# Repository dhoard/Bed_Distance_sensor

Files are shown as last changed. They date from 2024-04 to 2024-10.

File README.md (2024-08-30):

##  The Future of 3D printer Bed Leveling

[BDsensor](https://www.pandapi3d.com/bdsensor) is the first distance sensor that can work with 3D printer and do fast bed leveling and adjust z axis in real time.
it can measure the bed distance at any point in real time without moving the z axis up and down.

Faster leveling, realtime compensation, high accuracy.

1. No need to do probe points before every print, it will be automatically compensated for based on actual distance in real time.
 
2. You can do bed mesh leveling like a normal proximity sensor but much faster with this BDsensor.
   
3. Easy manual bed level adjustment thanks to ability to display the live sensor distance measurement on your screen.

Sensor type: inductive, eddy, can only measure the metal plate.

Range: 4mm (for different metal the range should be different, the normal pei steel plate is 4mm, but aluminum is about 2mm)

### Hardware:
* It can connect to most motherboards or GPIOs on the RaspberryPi
* Easy to install:
  small and light; can be installed anywhere, even surrounding metal above
* Support Can bus module
* Support high temperature chamber(120C) with the long cable probe [BDsensorM](https://github.com/markniu/Bed_Distance_sensor/wiki/BDsensor-M).
### Hardware Version
 . | hardware | firmware
--- | --- |---  
2022.6 | BDsensor VA, V1.0 | V1.0  
2023.4 | BDsensor VB, V1.1, the connector was changed | V1.1, support self reboot
2023.11 | BDsensor VB, V1.3, Upgrade the MCU to STM32 | V1.2, for stm32
2024.2  |              |V1.2c, [Support nozzle collision sensing](https://github.com/markniu/Bed_Distance_sensor/wiki/Collision-sensing)
2024.3  | BDsensorM V1.0             | V1.2c
2024.7  | BDsensorM V1.1             |  V1.2c, [Pins order](https://github.com/markniu/Bed_Distance_sensor/issues/178#issuecomment-2319621934) are changed in EXP1 connector

### Software
 . | Marlin | Klipper
--- | --- |---  
Real Time leveling(beta) |:heavy_check_mark:| :heavy_check_mark:  
Fast bed mesh |:heavy_check_mark:| :heavy_check_mark: 
Fast bed mesh(No toolhead stop)|:heavy_check_mark: | :heavy_check_mark: 
Distance display |:heavy_check_mark: | :heavy_check_mark: 
Can bus toolhead|No | :heavy_check_mark: 
standby mode automatic while printing|:heavy_check_mark: | :heavy_check_mark: 
[KAMP](https://github.com/kyleisah/Klipper-Adaptive-Meshing-Purging) Adaptive Meshing & Purging |No | :heavy_check_mark: 
nozzle collision sensing|[Detail](https://github.com/markniu/Bed_Distance_sensor/wiki/Collision-sensing-for-Marlin):heavy_check_mark:  | :heavy_check_mark: 

### Benefit of Collision sensing
1.  **Auto z offset calibration**.
2.  **Overcome the temperature drift**.
     The temperature drift will only change the z_offset, it will rise or low the whole bed mesh, but does not change the bed mesh with this BDsensor. that means the bed mesh is the same even with [different temperature](https://www.pandapi3d.com/post/nozzle-collision-sensing-with-bdsensor).
3. Repeatability: **+/-0.005mm**
4. No external hardware and easy to adjust

### Benefit of version M:

1.  For High temperature chamber up to [120C](https://github.com/markniu/Bed_Distance_sensor/wiki/BDsensor-M)
2.  The lightest probe, 1.5g

### Document  : [WiKi](https://github.com/markniu/Bed_Distance_sensor/wiki)

[History](https://hackaday.io/project/185096-0006mm-distance-resolution-sensor-for-3d-printer)

#### Mount STL:  [BLtouch_Compatible](https://www.thingiverse.com/thing:6098131) | [VzBoT](https://discord.com/channels/829828765512106054/1163237892957671424) | [Stealthburner Voron](https://www.printables.com/model/831679-lazy-bd-sensor-adapter-for-stealthburner-voron)

### Support
 https://www.facebook.com/groups/380795976169477

#### Where to buy:
 [pandapi3d.com](https://www.pandapi3d.com) , [elecrow](https://www.elecrow.com/bd-sensor.html) , [淘宝店](https://item.taobao.com/item.htm?spm=a1z10.1-c.w4004-14344044600.5.60a16ff77NRBL5&id=684572042388)

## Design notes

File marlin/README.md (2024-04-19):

Install marlin

https://github.com/markniu/Bed_Distance_sensor/wiki/Installing-Bed-Distance-Sensor

example: https://drive.google.com/drive/folders/13poitJhHradERgTLGtSDJb0zpuyNYHZY?usp=sharing

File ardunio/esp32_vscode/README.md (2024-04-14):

Arduino testing code

This is a simple arduino testing code. It read the distance data from BDsensor after initial the communication port.

If you want to do more code by yourself for other application here is the protocol of data 

https://github.com/markniu/Bed_Distance_sensor/wiki/Data-Protocol

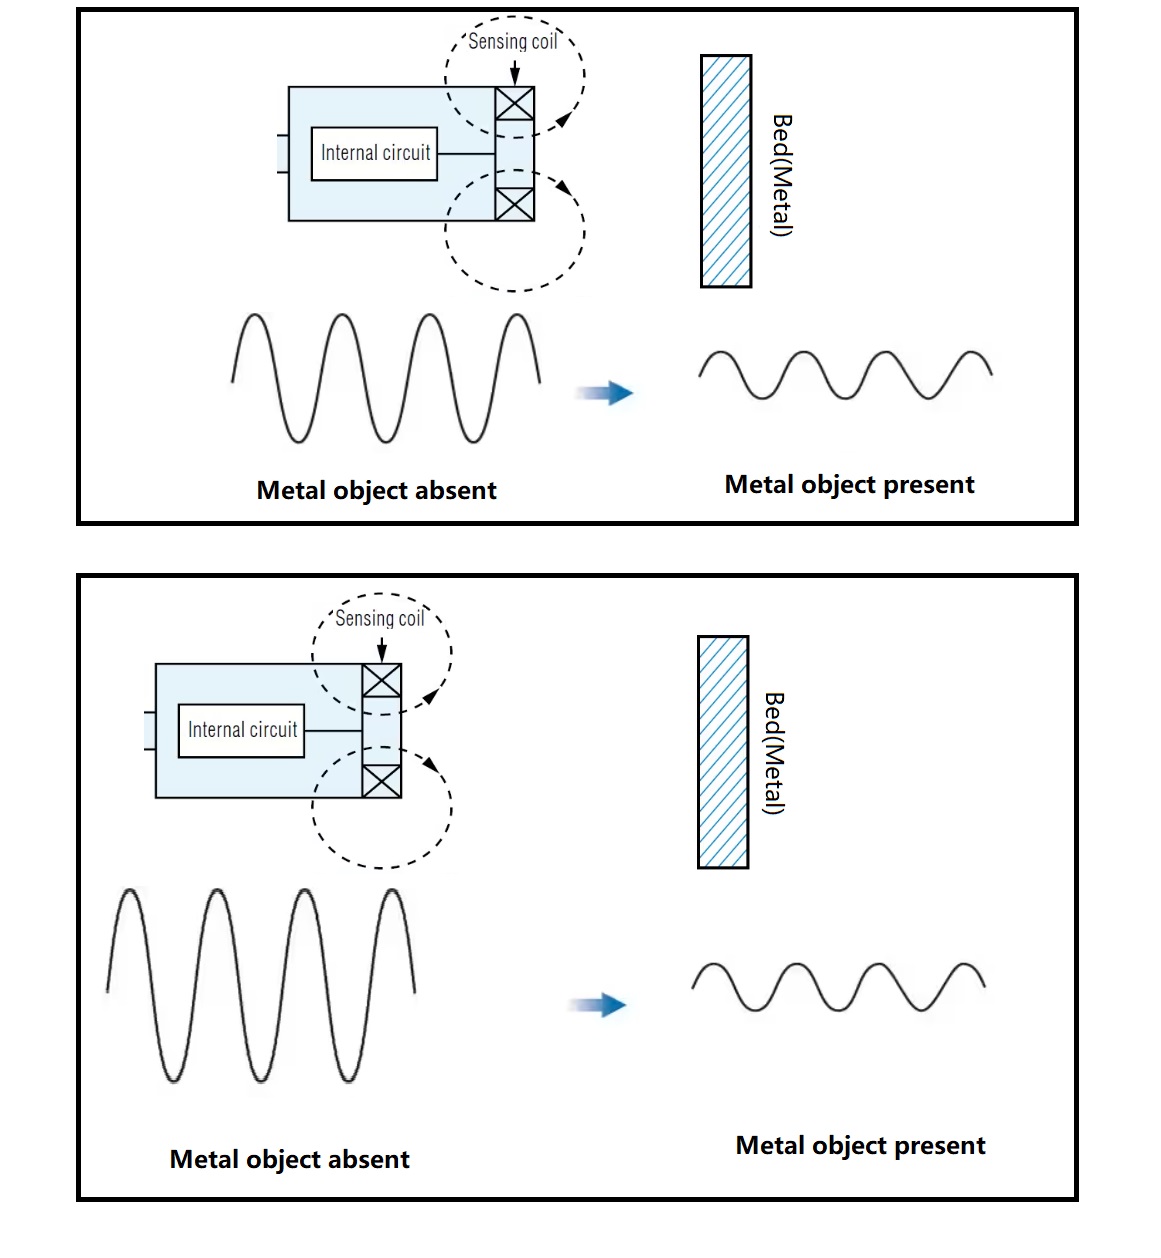
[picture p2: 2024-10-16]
doc/images/howwork.png

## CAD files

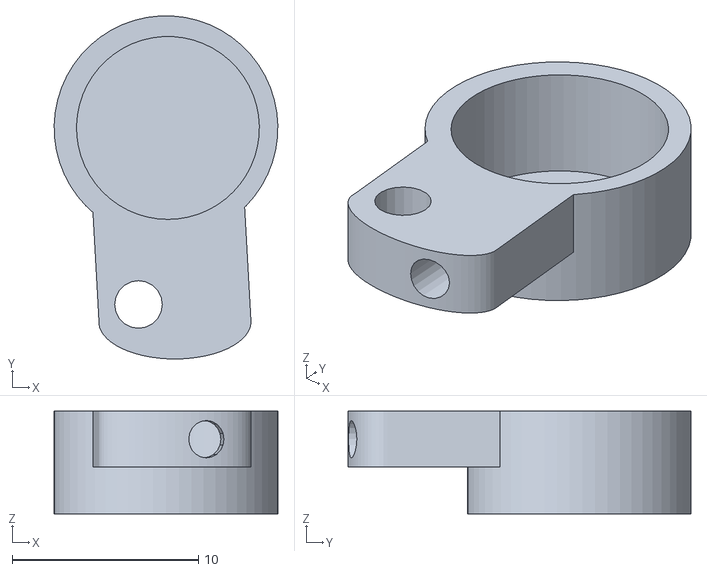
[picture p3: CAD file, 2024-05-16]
design/coil_case_without_coil.stl
12.0 x 18.4 x 5.50

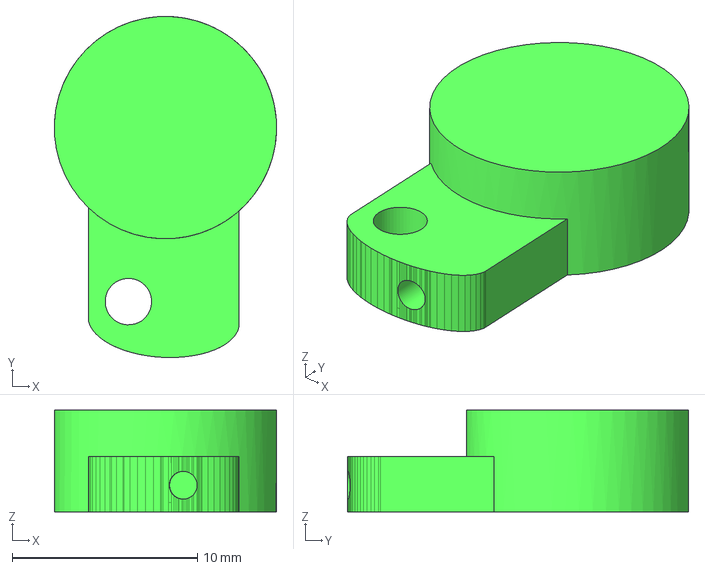
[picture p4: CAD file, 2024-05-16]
design/coil_case.step
12.0 x 18.4 x 5.50 mm

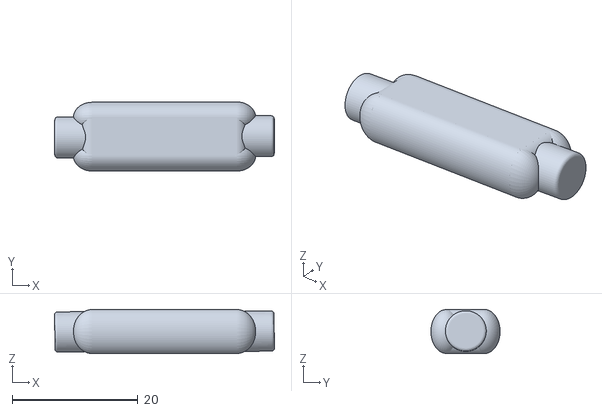
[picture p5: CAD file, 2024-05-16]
design/PCB_case.stl
35.0 x 11.0 x 7.00

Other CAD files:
design/coil_case.stl

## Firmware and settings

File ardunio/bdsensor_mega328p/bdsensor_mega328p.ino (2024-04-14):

#include <Arduino.h>
#include <U8g2lib.h>
#include "Panda_segmentBed_I2C.h"
#ifdef U8X8_HAVE_HW_SPI
#include <SPI.h>
#endif
#ifdef U8X8_HAVE_HW_I2C
#include <Wire.h>
#endif

I2C_SegmentBED BD_SENSOR_I2C;
#define  I2C_BED_SDA  12  
#define  I2C_BED_SCL  11  
#define DELAY 100
#define MAX_BD_HEIGHT 6.9
#define CMD_START_READ_CALIBRATE_DATA   1017
#define CMD_END_READ_CALIBRATE_DATA   1018
#define CMD_START_CALIBRATE 1019
#define CMD_END_CALIBRATE 1021  
#define CMD_READ_VERSION  1016
#define CMD_DISTANCD_RAWDATA_TYPE 1020       // switch output distance data type to raw data, default is mm (1 represent 0.01mm)

char tmp_1[50];
unsigned int n=0,i=0;
float Distance=0.0;

U8G2_SSD1306_128X32_UNIVISION_F_SW_I2C u8g2(U8G2_R0, /* clock=*/ SCL, /* data=*/ SDA, /* reset=*/ U8X8_PIN_NONE);  



void dis_text(char *tmp_d,char x,char y)
{
  
  u8g2.setFont(u8g2_font_ncenB08_tr); // choose a suitable font
  u8g2.drawStr(x,y,tmp_d);  // write something to the internal memory
  u8g2.sendBuffer();          // transfer internal memory to the display

}

unsigned short read_one_data()
{
    unsigned short tmp=0;
    tmp=BD_SENSOR_I2C.BD_i2c_read();    
    if(BD_SENSOR_I2C.BD_Check_OddEven(tmp)==0)
      //printf("CRC error!\n");
     // sprintf(tmp_1,"CRC error");
       tmp=1024;
    else
    {
      tmp=(tmp&0x3ff);
     // sprintf(tmp_1,"Distance:%.2f\n",Distance);
      //printf(tmp_1);
    }
    return tmp;
}

void read_version(char *txt)
{
  int i=0;
  BD_SENSOR_I2C.BD_i2c_write(CMD_READ_VERSION);
  for(i=0;i<20;i++)
      txt[i]=read_one_data();
  BD_SENSOR_I2C.BD_i2c_write(CMD_END_READ_CALIBRATE_DATA);
}


unsigned short read_raw_data(void)
{
  unsigned short tm=0;
  BD_SENSOR_I2C.BD_i2c_write(CMD_DISTANCD_RAWDATA_TYPE);
  tm=read_one_data();
  BD_SENSOR_I2C.BD_i2c_write(CMD_END_READ_CALIBRATE_DATA);
  return tm;
}

void setup(void) {
  u8g2.begin();
  u8g2.clearBuffer();          // clear the internal memory
  BD_SENSOR_I2C.i2c_init(I2C_BED_SDA,I2C_BED_SCL,0x3C,20);
  BD_SENSOR_I2C.BD_i2c_write(CMD_END_READ_CALIBRATE_DATA);
   //read and display version
  sprintf(tmp_1,"");
  read_version(tmp_1+strlen(tmp_1));
  dis_text(tmp_1,0,10);
  ///
  
}

void loop(void) {
  u8g2.clearBuffer(); 
  u8g2.setFont(u8g2_font_ncenB08_tr); // choose a suitable font
  //u8g2.drawStr(x,y,tmp_d);  // write something to the internal memory
  //u8g2.sendBuffer();   

  sprintf(tmp_1,"");
  read_version(tmp_1+strlen(tmp_1));
  //dis_text(tmp_1,0,10);
  u8g2.drawStr(0,10,tmp_1);
  
  //delay(10);  
  //read and display raw data
  n=read_raw_data();
  sprintf(tmp_1,"%d ",n);
  //dis_text(tmp_1,0,30);

  // read and display distance,but need to calibrate first
  Distance=read_one_data()/100.0;
  sprintf(tmp_1+strlen(tmp_1),", ");
  dtostrf(Distance, 5, 2, tmp_1+strlen(tmp_1));
  sprintf(tmp_1+strlen(tmp_1)," mm");
  u8g2.drawStr(0,30,tmp_1);
  u8g2.sendBuffer();
  //dis_text(tmp_1,0,30);

}

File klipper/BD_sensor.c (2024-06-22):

// Code for Bed Distance Sensor
// Mark yue<niujl123@sina.com>
// This file may be distributed under the terms of the GNU GPLv3 license.

#include <string.h>
#include <stdlib.h>
#include "board/gpio.h"
#include "board/irq.h"
#include "board/misc.h"
#include "command.h"
#include "sched.h"
#include "autoconf.h" // CONFIG_*
#include "basecmd.h" // oid_alloc
#include "board/gpio.h" // gpio_out_write
#include "board/irq.h" // irq_disable
#include "board/misc.h" // timer_is_before
#include "command.h" // DECL_COMMAND
#include "sched.h" // struct timer
#include "stepper.h" // stepper_event
#include "trsync.h" // trsync_add_signal

#define CMD_READ_DATA                 1015
#define CMD_READ_VERSION              1016
#define CMD_START_READ_CALIBRATE_DATA 1017
#define CMD_DISTANCE_MODE             1018
#define CMD_START_CALIBRATE           1019
#define CMD_END_CALIBRATE             1021
#define CMD_REBOOT_SENSOR             1022
#define CMD_SWITCH_MODE               1023
#define DATA_ERROR                    1024

#define CMD_Z_INDEX                    1025
#define CMD_CUR_Z                      1026
#define CMD_ADJ_Z                      1027
#define CMD_DIR_INV                    1028
#define CMD_STEP_MM                    1029
#define CMD_ZOID                       1030
#define CMD_RT_SAMPLE_TIME             1031
#define CMD_RT_RANGE                   1032


#define BYTE_CHECK_OK     0x01
#define BYTE_CHECK_ERR    0x00

#define BD_setLow(x)  gpio_out_write(x,0)
#define BD_setHigh(x) gpio_out_write(x,1)


uint8_t oid_g;
struct endstop {
    struct timer time;
    uint32_t rest_time, sample_time, nextwake,pin_num;
    struct trsync *ts;
    uint8_t flags, sample_count, trigger_count, trigger_reason;
    struct gpio_in pin;
};

enum { ESF_PIN_HIGH=1<<0, ESF_HOMING=1<<1 };

uint32_t delay_m = 20, homing_pose = 0;
int sda_pin = -1, scl_pin = -1, z_ofset = 0;
uint16_t BD_Data;
uint16_t BD_read_flag=CMD_DISTANCE_MODE;
int switch_mode = 0; //1:in switch mode
struct gpio_out sda_gpio, scl_gpio;
struct gpio_in sda_gpio_in;
static uint_fast8_t endstop_oversample_event(struct timer *t);
static struct endstop e ;

int z_index=0;
struct stepper {
    struct timer time;
    uint32_t interval;
    int16_t add;
    uint32_t count;
    uint32_t next_step_time, step_pulse_ticks;
    struct gpio_out step_pin, dir_pin;
    uint32_t position;
    struct move_queue_head mq;
    struct trsync_signal stop_signal;
    // gcc (pre v6) does better optimization when uint8_t are bitfields
    uint8_t flags : 8;
};
struct step_adjust{
    uint32_t cur_z;
    int adj_z_range;
    int invert_dir;
    int steps_per_mm;
    int step_time;
    int zoid;//oid for all the z stepper
};

#define NUM_Z_MOTOR  6
struct step_adjust step_adj[NUM_Z_MOTOR];//x,y,z
enum {
    SF_LAST_DIR=1<<0, SF_NEXT_DIR=1<<1, SF_INVERT_STEP=1<<2, SF_NEED_RESET=1<<3,
    SF_SINGLE_SCHED=1<<4, SF_HAVE_ADD=1<<5
};
struct endstop bd_tim ;

int32_t	diff_step=0,RT_SAMPLE_TIME=0,adjusted_step=0,RT_RANGE=1000;

int abs_bd(int a, int b){
 if (a > b)
    return a-b;
 else
 	return b-a;
}
extern void
command_config_stepper(uint32_t *args);
void adust_Z_live(uint16_t sensor_z);
void BD_i2c_write(unsigned int addr);
uint16_t BD_i2c_read(void);
void adust_Z_calc(uint16_t sensor_z,struct stepper *s);

void timer_bd_init(void);


int BD_i2c_init(uint32_t _sda,uint32_t _scl,
    uint32_t delays,uint32_t h_pose,int z_adjust)
{
    int i=0;
    sda_pin=_sda;
    scl_pin =_scl;
    homing_pose = h_pose;
    z_ofset = z_adjust;
    if (z_ofset > 500)
        z_ofset = 0;
    if(delays>0)
        delay_m=delays;
    sda_gpio=gpio_out_setup(sda_pin, 1);
    scl_gpio=gpio_out_setup(scl_pin, 1);

    gpio_out_write(sda_gpio, 1);
    gpio_out_write(scl_gpio, 1);
	for (i=0;i<NUM_Z_MOTOR;i++){
        step_adj[i].cur_z=0;
    	step_adj[i].zoid=0;
		step_adj[i].adj_z_range=0;
	}
    BD_i2c_write(CMD_REBOOT_SENSOR); //reset BDsensor
	////
 	if(CONFIG_CLOCK_FREQ>100000000)
		RT_SAMPLE_TIME= timer_from_us(11000);
	else if(CONFIG_CLOCK_FREQ>60000000)
		RT_SAMPLE_TIME= timer_from_us(16000);
	else //if(CONFIG_CLOCK_FREQ>60000000)
		RT_SAMPLE_TIME= timer_from_us(19000);
    return 1;
}

uint32_t nsecs_to_ticks_bd(uint32_t ns)
{
    return ns * (CONFIG_CLOCK_FREQ / 1000000);
}

void ndelay_bd_c(uint32_t nsecs)
{
   // if (CONFIG_MACH_AVR)
   //     return;
    uint32_t end = timer_read_time() + nsecs_to_ticks_bd(nsecs);
    while (timer_is_before(timer_read_time(), end));
       // irq_poll();
}

void ndelay_bd(uint32_t nsecs)
{
    int i=1;
    while(i--)
        ndelay_bd_c(nsecs);
}

unsigned short BD_Add_OddEven(unsigned short send_data)
{
    unsigned char i;
    unsigned char n;
    unsigned short out_data;
    n =0;
    for(i=0;i<10;i++){
        if(((send_data >>i)&0x01) == 0x01){
            n++;
        }
    }
    if((n&0x01) == 0x01){
        out_data = send_data | 0x400;
    }
    else{
        out_data = send_data | 0x00;
    }
    return out_data;
}

unsigned short BD_Check_OddEven(unsigned short rec_data)
{
    unsigned char i;
    unsigned char n;
    unsigned char ret;
    n =0;
    for(i=0;i<10;i++){
        if(((rec_data >>i)&0x01) == 0x01){
           n++;
        }
    }
    if((rec_data>>10) == (n&0x01)){
        ret = BYTE_CHECK_OK;
    }
    else{
        ret = BYTE_CHECK_ERR;
    }
    return ret;
}

void BD_I2C_start(void)
{
    sda_gpio=gpio_out_setup(sda_pin, 1);
    scl_gpio=gpio_out_setup(scl_pin, 1);
    BD_setHigh(scl_gpio);
    BD_setHigh(sda_gpio);
    ndelay_bd(delay_m);
    BD_setLow(sda_gpio);
    ndelay_bd(delay_m);
    BD_setLow(scl_gpio);
    ndelay_bd(delay_m);
}

void  BD_i2c_stop(void)
{
    ndelay_bd(delay_m);
    sda_gpio=gpio_out_setup(sda_pin, 1);
    BD_setLow(sda_gpio);
    ndelay_bd(delay_m);
    scl_gpio=gpio_out_setup(scl_pin, 1);
    BD_setHigh(scl_gpio);
    ndelay_bd(delay_m);

    BD_setHigh(sda_gpio);
    ndelay_bd(delay_m);
}

uint16_t BD_i2c_read(void)
{
    uint16_t b = DATA_ERROR;
    BD_I2C_start();
    BD_setHigh(sda_gpio);
    BD_setHigh(scl_gpio);
    ndelay_bd(delay_m);
    BD_setLow(scl_gpio);

    ndelay_bd(delay_m);
    b = 0;
    BD_setHigh(sda_gpio);
    sda_gpio_in=gpio_in_setup(sda_pin,0);
    for (unsigned char i = 0; i <= 10; i++) {
        b <<= 1;
        ndelay_bd(delay_m);
        BD_setHigh(scl_gpio);
		ndelay_bd(delay_m);
       // if (gpio_in_read(sda_gpio_in))
        b |= gpio_in_read(sda_gpio_in);
      //  ndelay_bd(delay_m);
        BD_setLow(scl_gpio);
    }
    BD_i2c_stop();
    if (BD_Check_OddEven(b) && (b & 0x3FF) < 1020){
        b = (b & 0x3FF);
        if(BD_read_flag==CMD_DISTANCE_MODE&&(b<1000)){
            b = b - z_ofset;
            if(b>DATA_ERROR)
                b=0;
        }

    }
    else
        b=DATA_ERROR;
 #if 0
    sda_gpio_in=gpio_in_setup(sda_pin,0);
    b=gpio_in_read(sda_gpio_in)*100;
 #endif
    return b;
}
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

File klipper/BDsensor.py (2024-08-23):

# Bed leveling sensor BDsensor(Bed Distance sensor)
# https://github.com/markniu/Bed_Distance_sensor
# Copyright (C) 2023 Mark yue <niujl123@sina.com>
# This file may be distributed under the terms of the GNU GPLv3 license.
import sched
import time
import copy
import chelper
import math
from threading import Timer
from mcu import MCU, MCU_trsync
from . import manual_probe
from . import probe
BD_TIMER = 0.600
TRSYNC_TIMEOUT = 0.025
TRSYNC_SINGLE_MCU_TIMEOUT = 0.250

CMD_READ_DATA = 1015
CMD_READ_VERSION = 1016
CMD_START_READ_CALIBRATE_DATA = 1017
CMD_DISTANCE_MODE = 1018
CMD_START_CALIBRATE = 1019
CMD_DISTANCE_RAWDATA_TYPE = 1020
CMD_END_CALIBRATE = 1021
CMD_REBOOT_SENSOR = 1022
CMD_SWITCH_MODE = 1023
DATA_ERROR = 1024

# Calculate a move's accel_t, cruise_t, and cruise_v
def calc_move_time(dist, speed, accel):
    axis_r = 1.
    if dist < 0.:
        axis_r = -1.
        dist = -dist
    if not accel or not dist:
        return axis_r, 0., dist / speed, speed
    max_cruise_v2 = dist * accel
    if max_cruise_v2 < speed ** 2:
        speed = math.sqrt(max_cruise_v2)
    accel_t = speed / accel
    accel_decel_d = accel_t * speed
    cruise_t = (dist - accel_decel_d) / speed
    return axis_r, accel_t, cruise_t, speed

# Helper to obtain a single probe measurement
def run_single_probe(probe, gcmd):
    probe_session = probe.start_probe_session(gcmd)
    probe_session.run_probe(gcmd)
    pos = probe_session.pull_probed_results()[0]
    probe_session.end_probe_session()
    return pos

# I2C BD_SENSOR
# devices connected to an MCU via an virtual i2c bus(2 any gpio)

HINT_TIMEOUT = """
If the probe did not move far enough to trigger, then
consider reducing the Z axis minimum position so the probe
can travel further (the Z minimum position can be negative).
"""


class BDPrinterProbe:
    def __init__(self, config, mcu_probe):
        self.printer = config.get_printer()
        self.name = config.get_name()
        self.config = config
        self.mcu_probe = mcu_probe
        self.speed = config.getfloat('speed', 5.0, above=0.)
        self.lift_speed = config.getfloat('lift_speed', self.speed, above=0.)
        self.x_offset = config.getfloat('x_offset', 0.)
        self.y_offset = config.getfloat('y_offset', 0.)
        self.z_offset = config.getfloat('z_offset')
        self.probe_calibrate_z = 0.
        self.multi_probe_pending = False
        self.rapid_scan = False
        self.last_state = False
        self.last_z_result = 0.
        self.homing_speed_tmp = 0
        self.gcode_move = self.printer.load_object(config, "gcode_move")
        # Infer Z position to move to during a probe
        if config.has_section('stepper_z'):
            zconfig = config.getsection('stepper_z')
            self.z_position = zconfig.getfloat('position_min', 0.,
                                               note_valid=False)
        else:
            pconfig = config.getsection('printer')
            self.z_position = pconfig.getfloat('minimum_z_position', 0.,
                                               note_valid=False)
        # Multi-sample support (for improved accuracy)
        self.sample_count = config.getint('samples', 1, minval=1)
        self.sample_retract_dist = config.getfloat('sample_retract_dist', 5.,
                                                   above=0.)
        self.samples_result = config.getchoice(
            'samples_result',
            {'median': 'median', 'average': 'average'},
            'average'
        )
        self.samples_tolerance = config.getfloat('samples_tolerance', 0.100,
                                                 minval=0.)
        self.samples_retries = config.getint('samples_tolerance_retries', 0,
                                             minval=0)
        # Register z_virtual_endstop pin
        self.printer.lookup_object('pins').register_chip('probe', self)

        # Register homing event handlers
        self.printer.register_event_handler("homing:homing_move_begin",
                                            self._handle_homing_move_begin)
        self.printer.register_event_handler("homing:homing_move_end",
                                            self._handle_homing_move_end)
        self.printer.register_event_handler("homing:home_rails_begin",
                                            self._handle_home_rails_begin)
        self.printer.register_event_handler("homing:home_rails_end",
                                            self._handle_home_rails_end)
        self.printer.register_event_handler("gcode:command_error",
                                            self._handle_command_error)
        # Register PROBE/QUERY_PROBE commands
        self.gcode = self.printer.lookup_object('gcode')
        self.gcode.register_command('PROBE', self.cmd_PROBE,
                                    desc=self.cmd_PROBE_help)
        self.gcode.register_command('QUERY_PROBE', self.cmd_QUERY_PROBE,
                                    desc=self.cmd_QUERY_PROBE_help)
        self.gcode.register_command('PROBE_CALIBRATE',
                                    self.cmd_PROBE_CALIBRATE,
                                    desc=self.cmd_PROBE_CALIBRATE_help)
        self.gcode.register_command('PROBE_ACCURACY', self.cmd_PROBE_ACCURACY,
                                    desc=self.cmd_PROBE_ACCURACY_help)
        self.gcode.register_command(
            'Z_OFFSET_APPLY_PROBE',
            self.cmd_Z_OFFSET_APPLY_PROBE,
            desc=self.cmd_Z_OFFSET_APPLY_PROBE_help
        )
        gcode = self.printer.lookup_object('gcode')
        self.dummy_gcode_cmd = gcode.create_gcode_command("", "", {})
        self.reactor = self.printer.get_reactor()
        self.bd_sample_timer = self.reactor.register_timer(
            self.scan_sample_event)
        
    def _probe_state_error(self):
        raise self.printer.command_error(
                "Internal probe error - start/end probe session mismatch")
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

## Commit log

2024-04-02 optimize the collision sensing in different bed area
    [BDsensor.py]
2024-04-04 increase the accuracy of collision sensing within 0.01mm
    [BDsensor.py]
2024-04-06 clean code of collision sensing
    [BDsensor.py]
2024-04-13 allow adjust if the collision sensing in the air sometime
    [BDsensor.py]
2024-04-14 collision sensing optimize : the constantly of z_offset within +-0.005
    [BDsensor.py]
2024-04-14 add using bdsensor as the width sensor; adding ardunio test project for mega328p
2024-04-19 add marlin example project code with BDsensor
    [Configuration.h, Configuration_adv.h]
2024-04-23 add an error message if there is no section bed_mesh
    [BDsensor.py]
2024-04-23 reverted the last change that will may cause error in some case
    [BDsensor.py]
2024-05-06 real time level bug: M84 error for CAN module printer
    [BDsensor.py]
2024-05-08 disable the timer if the Real time level is not enabled
2024-05-09 reverted the last change that will may cause z still trigered error
    [BD_sensor.c]
2024-05-12 disable collision probe while doing z tilt or quad gantry level, let collision only work when homing,
    [BDsensor.py]
2024-05-16 Added coil_case.step file. General cleanup
    [PCB_case.stl, coil_case.step, coil_case.stl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]
2024-05-19 Optimize the data for CAN bus: Combined some commands into one and reduce the command length, this change needs to compile and flash the klipper firmware
    1,Optimize the data for CAN bus: Combined some commands into one and reduce the command length, this change needs to compile and flash the klipper firmware
    2, Collision homing can be set by the gcode
    3, clear the code
    [BD_sensor.c, BDsensor.py]
2024-05-20 fix the enable error for Real_Time_Level and this update needs to compile & flash klipper.bin
    [BD_sensor.c, BDsensor.py]
2024-05-25 Real Time Level: add rt_sample_time in section BDsensor for fix the timer too close
    add rt_sample_time:16 #ms in BDsensor section
    [BD_sensor.c, BDsensor.py]
2024-06-01 Real Time Level: support multi Z printer
2024-06-02 Real Time Level: detect the nozzle collision while printing
    [BD_sensor.c]
2024-06-06 increase the trigger position to avoid crash
    [BDsensor.py]
2024-06-09 fix the command BDSENSOR_VERSION problem
    [BDsensor.py]
2024-06-12 sync code from the official klipper; add max range for Real time level
2024-06-15 sync code from official klipper
2024-06-15 sync the code of official klipper
2024-06-16 sync the code from official klipper probe.py
2024-06-16 sync the code from official klipper that updated today
2024-06-19 1)Sync code from klipper; 2)RealTimeLevel: smooth Z motor
2024-06-20 sync code from the latest official klipper
2024-06-22 RealTimeLevel: support z_offset adjust while printing
2024-06-22 fixed a new bug: no_stop_probe can't work by sync the code from klipper official
    [BDsensor.py]
2024-06-23 sync probe_calibrate code from the official klipper
2024-06-29 add a delay after calibrate the bdsensor to avoid error message on the console
    [BDsensor.py]
2024-06-30 fix a console error for some board
    [BDsensor.py]
2024-08-13 add z speed limit for sensor calibration
2024-08-14 add z adjust speed limit while doing collision sensing
    [BDsensor.py]
2024-08-23 Homing with contactless and contact probing together
    https://github.com/markniu/Bed_Distance_sensor/wiki/Homing-with-contactless-and-contact-probing-together
